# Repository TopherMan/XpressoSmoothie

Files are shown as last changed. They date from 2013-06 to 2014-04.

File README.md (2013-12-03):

Overview
========
This is a plan to make a RepRap electronics solution capable of running the Smoothie firmware. The board will be built around the LPCXpresso 1769, with a more modular design in the spirit of RAMPS. More information about the RepRap project can be found at http://reprap.org, and more information about Smoothie can be found at http://smoothieware.org.

Features
========
* 120 MHz ARM Cortex-M3 processor, chosen to run the highly efficent and modular Smoothie firmware (https://github.com/arthurwolf/Smoothie).
* Can be powered by 12V or 24V.
* 5 Axes, using Pololu A4988-style stepper drivers.
* 4 Power output MOSFETs, two with automotive blade-style fuses for bed and heater over-current protection.
* 6 endstops and 3 thermistors.
* Integrated microSD reader.
* Pins broken out for SPI, I2C, GPIO, and on-board Ethernet chip for future expansion.
* Due to the modular nature of Smoothie, the board should also work with mills, laser cutters, and any future modules.

Current Status
==============
Revision 0 boards had issues due to pins being assigned to ports hard-coded to other purposes in Smoothie. Revision 1 had issues due to pin assignment changes in the Smoothie firmware. Revision 2 is close to complete, with pinout verification needed.

Opto Endstops
=============
Noobman is finalizing designs for a small seperate opto board.

Bill of Materials -- NOTE: may need to be updated
=================
Two bill of material files are included. BOM.ods lists the individual components and their corresponding Digikey part numbers. BOM_Digikey.xls is formatted for uploading directly to Digikey. There are three columns available, one for the complete range of parts, one for everything except opto circuitry (though the difference is only 6 resistors), and one without opto circuitry or headers, so you can use big cheap strips of breakaway headers.

To Use
======
Assembly instructions will be made with the alpha board.
Flashing the bootloader and getting Smoothie on the LPCXpresso can be found at http://smoothieware.org/smoothie-on-a-breadboard.

More Information
================
Wiki page at http://reprap.org/wiki/Xpresso_Smoothie.

Authors
=======
TopherMan (Chris George) -- Initial design idea and basic layout, as well as testing and assembly.
Noobman -- Significant input on design, and completed nearly all routing.
Bobc -- kicad libraries are borrowed from his repo here: https://github.com/bobc/bobc_hardware Additionally, blade fuse usage based on his design for RAMPS_FD

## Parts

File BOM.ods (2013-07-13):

Reference | Value | Footprint | Digikey | Alternate Piece
C1 | 100u | c_elec_6.3x7.7 | PCE4238CT-ND
C2 | 100u | c_elec_6.3x7.7 | PCE4238CT-ND
C3 | 100u | c_elec_6.3x7.7 | PCE4238CT-ND
C4 | 100u | c_elec_6.3x7.7 | PCE4238CT-ND
C5 | 1u/50v | SM1206 | 1276-1068-1-ND
C6 | 1u/50v | SM1206 | 1276-1068-1-ND
C7 | 1u/50v | SM1206 | 1276-1068-1-ND
C8 | 1u/50v | SM1206 | 1276-1068-1-ND
C9 | 10u | c_elec_4x5.3 | PCE3878CT-ND
C10 | 10u | c_elec_4x5.3 | PCE3878CT-ND
C11 | 10u | c_elec_4x5.3 | PCE3878CT-ND
C12 | 100u | c_elec_6.3x7.7 | PCE4238CT-ND
C13 | 100u | c_elec_6.3x7.7 | PCE4238CT-ND
C14 | 100u | c_elec_6.3x7.7 | PCE4238CT-ND
C15 | 220n | SM0805 | 1276-2948-1-ND
C16 | 220n | SM0805 | 1276-2948-1-ND
C17 | 220n | SM0805 | 1276-2948-1-ND
C18 | 220n | SM0805 | 1276-2948-1-ND
C19 | 220n | SM0805 | 1276-2948-1-ND
C20 | 220n | SM0805 | 1276-2948-1-ND
C21 | 220n | SM0805 | 1276-2948-1-ND
C22 | 1u/50v | SM1206 | 1276-1068-1-ND
C23 | 1u/50v | SM1206 | 1276-1068-1-ND
C24 | 1u/50v | SM1206 | 1276-1068-1-ND
D1 | 1N4007 | DO-41 | 641-1312-1-ND
D2 | 1N4007 | DO-41 | 641-1312-1-ND
D3 | POWER_1 | LED_0805 | 475-1415-1-ND
D4 | POWER_2 | LED_0805 | 475-1415-1-ND
D5 | POWER_3 | LED_0805 | 475-1415-1-ND
D6 | POWER_4 | LED_0805 | 475-1415-1-ND
D7 | 1N4007 | DO-41 | 641-1312-1-ND
D8 | 1N4007 | DO-41 | 641-1312-1-ND
D10 | V_IN | LED_0805 | 475-1410-1-ND
D11 | V_GATES | LED_0805 | 475-1410-1-ND
D12 | 3V3 | LED_0805 | 475-1410-1-ND
F1 | FUSE | MF-R1100 | RGEF1100-ND
F2 | FUSE | MF-R500 | MF-R500-ND
J1 | HEADER_4 | PIN_ARRAY_4x1 | 3M9449-ND
J2 | HEADER_4 | PIN_ARRAY_4x1 | 3M9449-ND
J3 | HEADER_3 | PIN_ARRAY_3x1 | 3M9448-ND
J4 | HEADER_3X2 | PIN_ARRAY_3x2 | 3M9459-ND
J5 | HEADER_3X2 | PIN_ARRAY_3x2 | 3M9459-ND
J6 | LPCXPRESSO | 2X PIN_ARRAY 27X1 | SAM1213-27-ND
 |  |  | SAM1213-27-ND
J7 | HEADER_4 | PIN_ARRAY_4x1 | 3M9449-ND
J8 | HEADER_4 | PIN_ARRAY_4x1 | 3M9449-ND
J9 | HEADER_3X2 | PIN_ARRAY_3x2 | 3M9459-ND
J10 | HEADER_3X2 | PIN_ARRAY_3x2 | 3M9459-ND
J11 | Pwr_in | Power Block | WM7855-ND | WM7847-ND
J12 | HEADER_4 | PIN_ARRAY_4x1 | 3M9449-ND
J13 | HEADER_4X2 | pin_array_4x2 | 3M9458-ND
J14 | HEADER_3X2 | PIN_ARRAY_3x2 | 3M9459-ND
J15 | HEADER_4 | PIN_ARRAY_4x1 | 3M9449-ND
J16 | HEADER_4 | PIN_ARRAY_4x1 | 3M9449-ND
J17 | HEADER_4 | PIN_ARRAY_4x1 | 3M9449-ND
J18 | HEADER_4 | PIN_ARRAY_4x1 | 3M9449-ND
J19 | HEADER_2 | LARGE_2x1 | WM7853-ND
J20 | HEADER_2 | LARGE_2x1 | WM7853-ND
J21 | HEADER_2 | LARGE_2x1 | WM7853-ND
J22 | HEADER_2 | LARGE_2x1 | WM7853-ND
J23 | HEADER_4 | PIN_ARRAY_4x1 | 3M9449-ND
J24 | HEADER_4 | PIN_ARRAY_4x1 | 3M9449-ND
J25 | HEADER_4 | PIN_ARRAY_4x1 | 3M9449-ND
J26 | USB | USB_MICRO | 609-4048-1-ND
J27 | HEADER_4 | PIN_ARRAY_4x1 | 3M9449-ND
J28 | CONN_MICROSD | MICROSD | H11610CT-ND
 | HEADER_4 | PIN_ARRAY_4x1 | 3M9449-ND
J172 | HEADER_2 | PIN_ARRAY_2x1 | 3M9447-ND
J232 | HEADER_2 | PIN_ARRAY_2x1 | 3M9447-ND
J252 | HEADER_2 | PIN_ARRAY_2x1 | 3M9447-ND
JP1 | HEADER_2 | PIN_ARRAY_2x1 | 3M9447-ND
JP2 | HEADER_2 | PIN_ARRAY_2x1 | 3M9447-ND
JP3 | HEADER_2 | PIN_ARRAY_2x1 | 3M9447-ND
JP4 | HEADER_2 | PIN_ARRAY_2x1 | 3M9447-ND
 | HEADER_2 | PIN_ARRAY_2x1 | 3M9447-ND
 | HEADER_2 | PIN_ARRAY_2x1 | 3M9447-ND
 | HEADER_2 | PIN_ARRAY_2x1 | 3M9447-ND
 | HEADER_2 | PIN_ARRAY_2x1 | 3M9447-ND
JP5 | HEADER_2 | PIN_ARRAY_2x1 | 3M9447-ND
Q1 | IRLB 8743 | TO-220 | IRLB8743PBF-ND
Q2 | IRLB 8743 | TO-220 | IRLB8743PBF-ND
Q3 | IRLB 8743 | TO-220 | IRLB8743PBF-ND
Q4 | IRLB 8743 | TO-220 | IRLB8743PBF-ND
R1 | 4k7 | SM0805 | RHM4.70KAECT-ND
R2 | 4k7 | SM0805 | RHM4.70KAECT-ND
R3 | 1k | SM0805 | RHM1.0KKCT-ND
R4 | 1k | SM0805 | RHM1.0KKCT-ND
R5 | 4k7 | SM0805 | RHM4.70KAECT-ND
R6 | 4k7 | SM0805 | RHM4.70KAECT-ND
R7 | 100r | SM0805 | RHM100KCT-ND
R8 | 1k | SM0805 | RHM1.0KKCT-ND
R9 | 1k | SM0805 | RHM1.0KKCT-ND
R10 | 4k7 | SM0805 | RHM4.70KAECT-ND
R11 | 4k7 | SM0805 | RHM4.70KAECT-ND
R12 | 4k7 | SM0805 | RHM4.70KAECT-ND
R13 | 4k7 | SM0805 | RHM4.70KAECT-ND
R14 | 1k | SM0805 | RHM1.0KKCT-ND
R15 | 100r | SM0805 | RHM100KCT-ND
R16 | 100r | SM0805 | RHM100KCT-ND
R18 | 1k8 | SM0805 | RHM1.8KKCT-ND
R19 | 1k8 | SM0805 | RHM1.8KKCT-ND
R21 | 1k8 | SM0805 | RHM1.8KKCT-ND
R23 | 1k8 | SM0805 | RHM1.8KKCT-ND
R24 | 100r | SM0805 | RHM100KCT-ND
R25 | 100r | SM0805 | RHM100KCT-ND
R28 | 1k8 | SM0805 | RHM1.8KKCT-ND
R29 | 680r | SM0805 | RHM680KCT-ND
R30 | 100r | SM0805 | RHM100KCT-ND
RL_diode1 | 100r | SM0805 | RHM100KCT-ND | Values may change based on opto used
RL_diode2 | 100r | SM0805 | RHM100KCT-ND | Values may change based on opto used
RL_diode3 | 100r | SM0805 | RHM100KCT-ND | Values may change based on opto used
Rp_rcv1 | 1k5 | SM0805 | RHM1.5KKCT-ND | Values may change based on opto used
Rp_rcv2 | 1k5 | SM0805 | RHM1.5KKCT-ND | Values may change based on opto used
Rp_rcv3 | 1k5 | SM0805 | RHM1.5KKCT-ND | Values may change based on opto used
SW1 | SW_PUSH | SW_PUSH_SMALL | 450-1642-ND
SW2 | SW_PUSH | SW_PUSH_SMALL | 450-1642-ND
 | SW_PUSH | SW_PUSH_SMALL | 450-1650-ND
Th0 | CONN_2 | PIN_ARRAY_2x1 | 3M9447-ND
Th1 | CONN_2 | PIN_ARRAY_2x1 | 3M9447-ND
Th2 | CONN_2 | PIN_ARRAY_2x1 | 3M9447-ND
U1 | POLOLU_A4988 | 2X PIN_ARRAY 8X1 | S7006-ND
 |  |  | S7006-ND
U2 | POLOLU_A4988 | 2X PIN_ARRAY 8X1 | S7006-ND
 |  |  | S7006-ND
U3 | POLOLU_A4988 | 2X PIN_ARRAY 8X1 | S7006-ND
 |  |  | S7006-ND
U4 | POLOLU_A4988 | 2X PIN_ARRAY 8X1 | S7006-ND
 |  |  | S7006-ND
U5 | POLOLU_A4988 | 2X PIN_ARRAY 8X1 | S7006-ND
 |  |  | S7006-ND
U7 | LM7809CT | TO-220 | LM7809CT-ND
U8 | TC4422A | SO8N | TC4422AVOA-ND
U9 | TC4422A | SO8N | TC4422AVOA-ND
U10 | TC4422A | SO8N | TC4422AVOA-ND
U11 | TC4422A | SO8N | TC4422AVOA-ND
U12 | LM1117-3.3 | SOT223 | LM1117IMPX-3.3/NOPBCT-ND
 | Jumpers | 2 pos | A26228-ND | You'll need 19 for full microstepping on all 5 axes and all mcu jumpers set for LPCXpresso and 20 for mbed

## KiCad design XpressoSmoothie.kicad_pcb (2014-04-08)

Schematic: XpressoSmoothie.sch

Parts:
C1, C2, C3, C4, C12, C13, C14: 100u
C5, C7, C23, C24: 1u/50v
C6, C8: 1u/50v; SM1206
C9, C10, C11: 10u
C15, C16, C17, C18, C19, C20, C21: 220n
C22: 1u; SM1206
D1, D2, D7, D8: 1N4007
D3: POWER_1
D4: POWER_2
D5: POWER_3
D6: POWER_4
D9: LED4
D11: V_GATES
D12: 3V3
D13: LED2
D14: LED3
D15: LED1
F1, F2: FUSE
Hole1, Hole2, Hole3, Hole4: CONN_1
J1, J2, J7, J8, J12, J15, J27, J29, J30: HEADER_4
J3, J16, J17, J18, J23, J24, J25: HEADER_3
J4, J5, J9, J10, J14: HEADER_3X2
J6: LPCXPRESSO_1769_HEADER
J11: Pwr_in
J13: HEADER_6
J19, J20, J21, J22: HEADER_2
J26: USB
J28: MICROSD-MOLEX
M1: LOGO_OSHW; OSHW_logo_large
M2: LOGO_OSHW; OSHW_logo_10
Q1, Q2, Q3, Q4: IRLB 8743
R1, R2, R5, R6, R10, R11, R12, R13: 4k7
R3, R4, R8, R9, R14: 1k
R7, R15, R16, R17, R20, R22, R24, R25, R26, R30: 100
R18, R19, R21, R23: 1k8
R27, R28, R31, R32: 10k
R29: 680
SW1, SW2, SW3: SW_PUSH
Th0, Th1, Th2: CONN_2
U1, U2, U3, U4, U5: POLOLU_A4988
U7: LM7809CT; TO-220
U8, U9, U10, U11: TC4422A
U12: LM1117-3.3; TO-220

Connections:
*32_RD-: J6.32, J27.4
*33_RD+: J6.33, J27.3
*34_TD-: J6.34, J27.2
*35_TD+: J6.35, J27.1
*Bootloader: J6.51, SW3.1
*CS: J6.8, J28.2
*CS0: J6.14, J30.4
*LED1: J6.101, R20.2
*LED2: J6.102, R26.2
*LED3: J6.103, R17.2
*LED4: J6.104, R22.2
*MISO: J6.6, J28.7
*MISO0: J6.12, J30.2
*MOSI: J6.5, J28.3
*MOSI0: J6.11, J30.1
*PLAY/PAUSE: J6.53, SW2.1
*PLAY_LED: J6.115
*RESET: J6.4, SW1.1
*RX: J6.21, J29.4
*SCK: J6.7, J28.5
*SCK0: J6.13, J30.3
*SCL0: J6.26, J15.4
*SDA0: J6.25, J15.3
*THERM0: C11.1, J6.15, R12.1, Th0.1
*THERM1: C10.1, J6.16, R11.1, Th1.1
*THERM2: C9.1, J6.17, R10.1, Th2.1
*TX: J6.22, J29.3
*USB-D+: J6.37, J26.3 (D+)
*USB-D-: J6.36, J26.2 (D-)
*USB_SOFT_CONNECT: J6.119
+3.3VP: C14.1, C16.1, C22.1, J6.28, J15.1, J16.1, J17.1, J18.1, J23.1, J24.1, J25.1, J28.4, J29.2, R3.2, R4.2, R7.1, R8.2, R9.2, R10.2, R11.2, R12.2, R14.2, R15.1, R16.1, R24.1, R25.1, R30.2, U12.2 (OUT)
+5V: J3.3, J13.1, J26.1 (Vbus)
/THERM3: J6.18
A-DIR: J6.38, U5.16 (DIR)
A-EN: J6.39, R13.2, U5.9 (EN)
A-STEP: J6.42, U5.15 (STEP)
B-DIR: J6.117, U1.16 (DIR)
B-EN: J6.116, R1.2, U1.9 (EN)
B-STEP: J6.50, U1.15 (STEP)
BUZZ: J6.20, J13.5
CLICK: J6.19, J13.3
ENC_A: J6.105, J13.6
ENC_B: J6.106, J13.4
GND: C1.2, C2.2, C3.2, C4.2, C8.2, C9.2, C10.2, C11.2, C12.2, C13.2, C14.2, C15.2, C16.2, C17.2, C18.2, C19.2, C20.2, C21.2, C22.2, D9.2 (K), D12.2 (K), D13.2 (K), D14.2 (K), D15.2 (K), J6.1, J6.54, J11.3, J15.2, J16.2, J17.2, J18.2, J23.2, J24.2, J25.2, J26.4 (GND), J26.5 (Shield_1), J26.6 (Shield_2), J28.6, J28.GND, J28.POL, J29.1, R27.1, R28.1, R31.1, R32.1, SW1.2, SW2.2, SW3.2, Th0.2 (PM), Th1.2 (PM), Th2.2 (PM), U1.1 (GND), U1.7 (GND), U2.1 (GND), U2.7 (GND), U3.1 (GND), U3.7 (GND), U4.1 (GND), U4.7 (GND), U5.1 (GND), U5.7 (GND), U7.2 (GND), U12.1 (ADJ)
GNDPWR: C5.2, C6.2, C7.2, C23.2, C24.2, J11.2, Q1.S, Q2.S, Q3.S, Q4.S, R29.1, U8.4 (GND), U8.5 (GND), U9.4 (GND), U9.5 (GND), U10.4 (GND), U10.5 (GND), U11.4 (GND), U11.5 (GND)
unnamed: J10.5, U4.12 (MS3)
unnamed: J10.1, U4.10 (MS1)
unnamed: J8.4, U4.6 (2B)
unnamed: J8.1, U4.3 (IB)
unnamed: J8.2, U4.4 (1A)
unnamed: J8.3, U4.5 (2A)
unnamed: J10.3, U4.11 (MS2)
unnamed: J14.2, J14.4, J14.6, R13.1, R14.1, U5.13 (RST), U5.14 (SLP)
unnamed: J10.2, J10.4, J10.6, R6.1, R9.1, U4.13 (RST), U4.14 (SLP)
unnamed: J14.5, U5.12 (MS3)
unnamed: J14.1, U5.10 (MS1)
unnamed: J12.4, U5.6 (2B)
unnamed: J12.1, U5.3 (IB)
unnamed: J12.2, U5.4 (1A)
unnamed: J12.3, U5.5 (2A)
unnamed: J14.3, U5.11 (MS2)
unnamed: D2.1 (A), D4.2 (K), J20.1, Q2.D
unnamed: Q2.G, U9.6 (OUT), U9.7 (OUT)
unnamed: D4.1 (A), R21.2
unnamed: J5.2, J5.4, J5.6, R2.1, R4.1, U2.13 (RST), U2.14 (SLP)
unnamed: D1.1 (A), D3.2 (K), J19.1, Q1.D
unnamed: Q1.G, U8.6 (OUT), U8.7 (OUT)
unnamed: D3.1 (A), R19.2
unnamed: J9.5, U3.12 (MS3)
unnamed: J9.1, U3.10 (MS1)
unnamed: J7.4, U3.6 (2B)
unnamed: J7.1, U3.3 (IB)
unnamed: J7.2, U3.4 (1A)
unnamed: J7.3, U3.5 (2A)
unnamed: J9.3, U3.11 (MS2)
unnamed: J9.2, J9.4, J9.6, R5.1, R8.1, U3.13 (RST), U3.14 (SLP)
unnamed: J5.5, U2.12 (MS3)
unnamed: J5.1, U2.10 (MS1)
unnamed: J2.4, U2.6 (2B)
unnamed: J2.1, U2.3 (IB)
unnamed: J2.2, U2.4 (1A)
unnamed: J2.3, U2.5 (2A)
unnamed: J5.3, U2.11 (MS2)
unnamed: D9.1 (A), R22.1
unnamed: D14.1 (A), R17.1
unnamed: D13.1 (A), R26.1
unnamed: D15.1 (A), R20.1
unnamed: J3.2, U12.3 (IN)
unnamed: F1.2, J19.2
unnamed: F2.2, J20.2
unnamed: D11.2 (K), R29.2
unnamed: D6.2 (K), D7.1 (A), J22.1, Q4.D
unnamed: Q4.G, U10.6 (OUT), U10.7 (OUT)
unnamed: D6.1 (A), R18.2
unnamed: D5.2 (K), D8.1 (A), J21.1, Q3.D
unnamed: Q3.G, U11.6 (OUT), U11.7 (OUT)
unnamed: D5.1 (A), R23.2
unnamed: D12.1 (A), R30.1
unnamed: J4.5, U1.12 (MS3)
unnamed: J4.1, U1.10 (MS1)
unnamed: J1.4, U1.6 (2B)
unnamed: J1.1, U1.3 (IB)
unnamed: J1.2, U1.4 (1A)
unnamed: J1.3, U1.5 (2A)
unnamed: J4.3, U1.11 (MS2)
unnamed: J4.2, J4.4, J4.6, R1.1, R3.1, U1.13 (RST), U1.14 (SLP)
unnamed: R15.2, U2.2 (VDD)
unnamed: R16.2, U3.2 (VDD)
unnamed: R24.2, U4.2 (VDD)
unnamed: R25.2, U5.2 (VDD)
unnamed: R7.2, U1.2 (VDD)
PANEL_KILL: J6.52, J13.2
POWER1: J6.49, R27.2, U8.2 (IN)
POWER2: J6.48, R28.2, U9.2 (IN)
POWER3: J6.47, R31.2, U11.2 (IN)
POWER4: J6.113, R32.2, U10.2 (IN)
PS-ON: J6.46
SD_card_detect: J28.DET
Vgates: C5.1, C7.1, C13.1, C15.1, C23.1, C24.1, D11.1 (A), J3.1, U7.3 (OUT), U8.1 (VDD), U8.8 (VDD), U9.1 (VDD), U9.8 (VDD), U10.1 (VDD), U10.8 (VDD), U11.1 (VDD), U11.8 (VDD)
Vin_Hi_curr: C6.1, D1.2 (K), D2.2 (K), D7.2 (K), D8.2 (K), F1.1, F2.1, J11.1, J21.2, J22.2, R18.1, R19.1, R21.1, R23.1
Vin_rmot: C1.1, C2.1, C3.1, C4.1, C8.1, C12.1, C17.1, C18.1, C19.1, C20.1, C21.1, J11.4, U1.8 (VMOT), U2.8 (VMOT), U3.8 (VMOT), U4.8 (VMOT), U5.8 (VMOT), U7.1 (IN)
X-DIR: J6.118, U2.16 (DIR)
X-EN: J6.27, R2.2, U2.9 (EN)
X-STEP: J6.45, U2.15 (STEP)
XMAX: J6.108, J24.3
XMIN: J6.107, J17.3
Y-DIR: J6.23, U3.16 (DIR)
Y-EN: J6.24, R5.2, U3.9 (EN)
Y-STEP: J6.44, U3.15 (STEP)
YMAX: J6.114, J25.3
YMIN: J6.109, J18.3
Z-DIR: J6.40, U4.16 (DIR)
Z-EN: J6.41, R6.2, U4.9 (EN)
Z-STEP: J6.43, U4.15 (STEP)
ZMAX: J6.110, J23.3
ZMIN: J6.111, J16.3

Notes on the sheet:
POWER
MOSFETS
Output connectors are V+ and GND. Q1 is bed mosfet to keep high current trace short. Solder a thick copper wire from input to Q1 and back.
Enstops and Thermistors
STEPPER DRIVERS
SD card
I2C
Expansion
USB
Miscellaneous
Pololu drivers or compatible footprint: http://www.pololu.com/catalog/category/120
MOS drivers TC4452 (SOIC-8-Narrow) or TC4422A (SOIC-8-WIDE), check and adjust pcb footprint if needed.
Components: all smd ceramic caps dielectric X5R or X7R or better, leds: 20mA. Mosfet output connectors are V+ and GND. Q1 is bed mosfet to keep high current trace short. Solder a thick copper wire from input to Q1 and back (both on V+ and gnd) to help with the high current. For DIY purposes increas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
LPCXpresso 1769
Power in: 12V to 28V The two input connector voltages must come from same psu (same gnd), though may have different values.
Vin_Hi_curr does not have led indicator
Regulators have different pin numbering If Vin_r is 12V then Vgates are 12V-2Vdroput= 10V
Ethernet
Serial
*NOTE: Labels starting with * are hard-coded to a specific use and cannot be reassigned.
NOTE: Pins 9 and 10 are hard-coded in Smoothie for I2C communication with current-sense chips.
SPI
PANEL
LED1 init done, LED2 main loop LED3 idle loop, LED4 SD okay

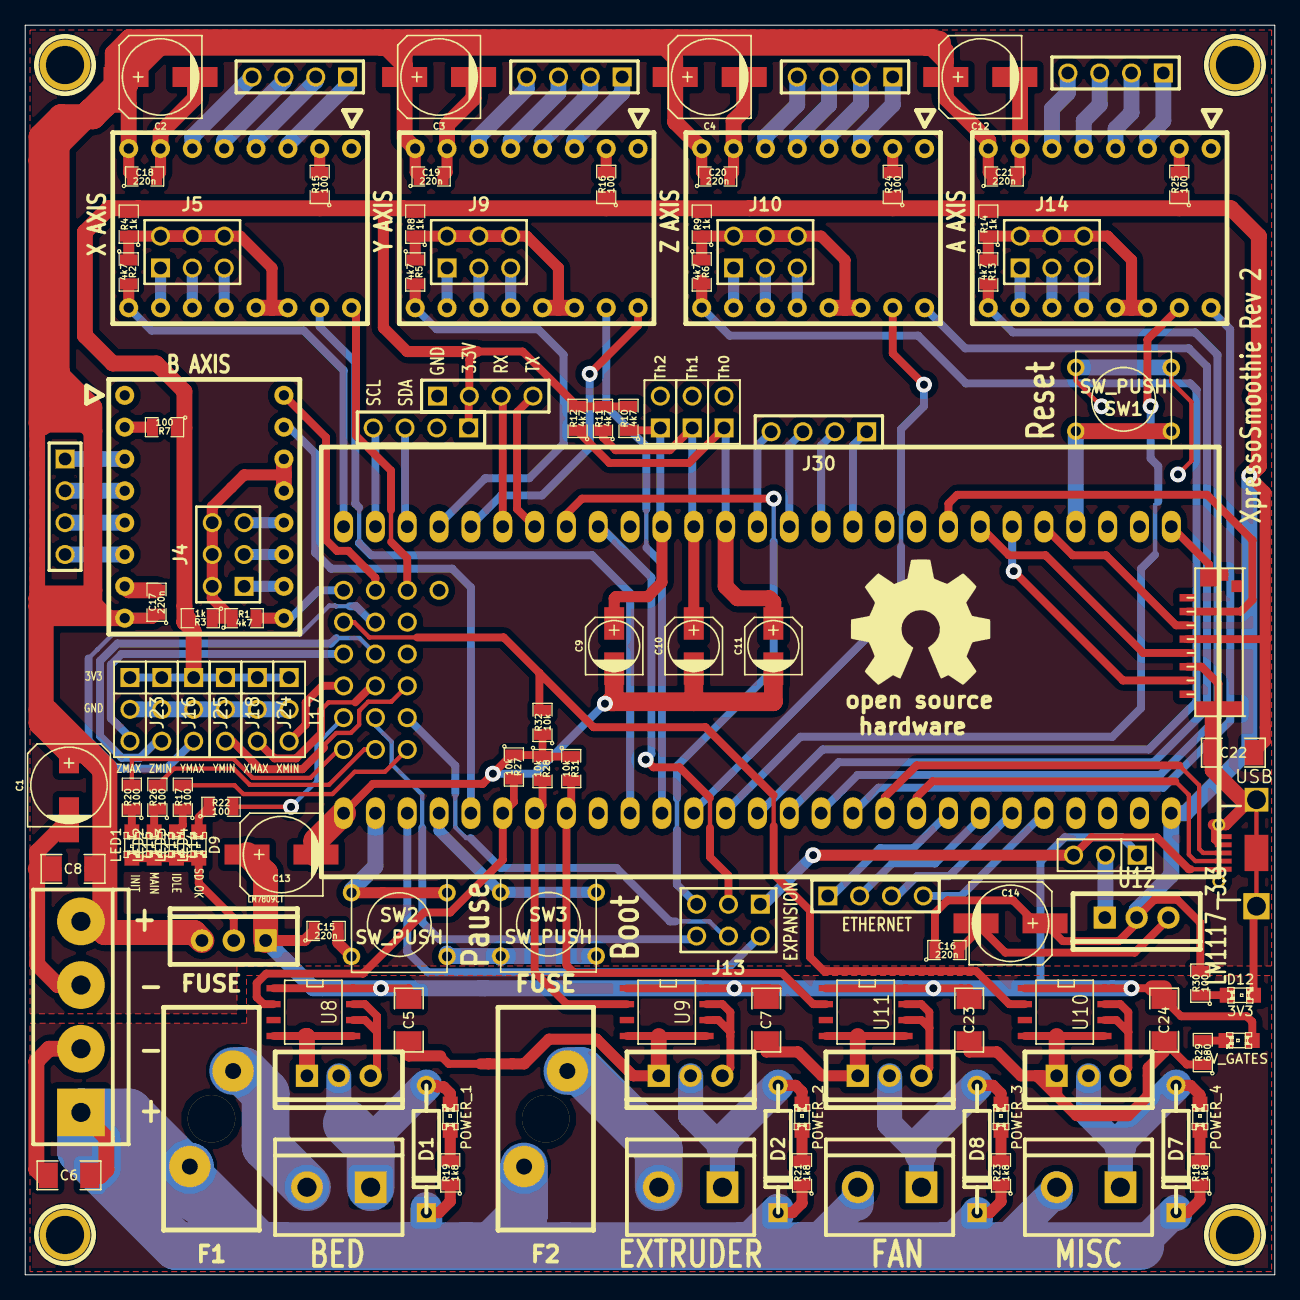
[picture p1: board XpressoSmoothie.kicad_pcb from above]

Board: 2 copper layers, 99.7 x 99.7 mm, 129 parts (1 on the bottom side), 131 nets.

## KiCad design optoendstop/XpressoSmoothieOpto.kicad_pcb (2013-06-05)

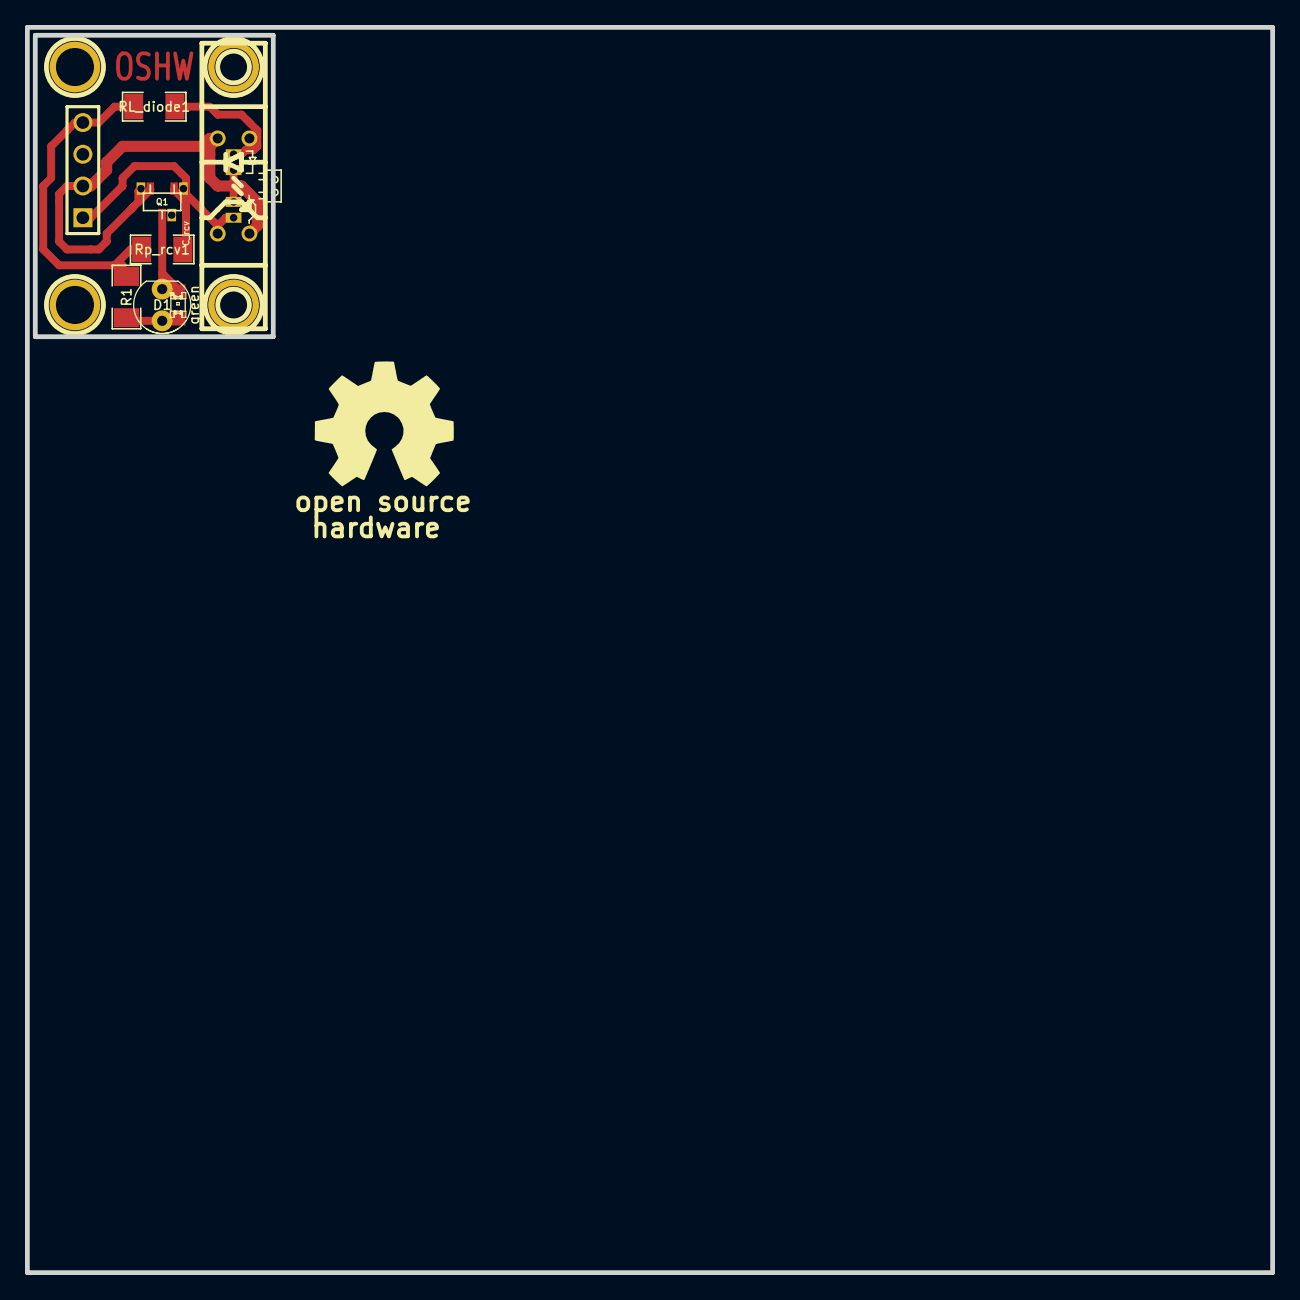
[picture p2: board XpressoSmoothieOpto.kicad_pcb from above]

Board: 2 copper layers, 99.7 x 99.7 mm, 13 parts (0 on the bottom side), 6 nets.

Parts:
D1: green; LED-0805-3MM
Hole1, Hole2, Hole3, Hole4: CONN_1; 1pin
IC1: TCST1103; TCST1103-2103
IC11: TCST1103; TCRT1000
J1: HEADER_4; PIN_ARRAY_4x1
M2: LOGO_OSHW; OSHW_logo_2
Q1: BS108D; sot23-to92
R1: 150; SM1206
RL_diode1: 68; SM1206
Rp_rcv1: 1k5; SM1206

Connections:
3.3V: J1.4, R1.2, RL_diode1.2, Rp_rcv1.1
GND: IC1.E/D, IC1.K/E, IC11.E/D, IC11.K/E, J1.2, Q1.S
unnamed: D1.1, R1.1
unnamed: D1.2, Q1.D
unnamed: IC1.A/+, IC11.A/+, RL_diode1.1
Signal1: IC1.C/+, IC11.C/+, J1.1, Q1.G, Rp_rcv1.2

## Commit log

2013-05-12 Initial commit. Schematic only missing mosfets.
    [XpressoSmoothie.sch]
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2013-05-13 Switch around pins and add pins for UART. Finish most of netlist.
    [XpressoSmoothie.brd, XpressoSmoothie.sch]
2013-05-13 Minor tag issues.
    [XpressoSmoothie.sch]
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2013-05-14 Add screw terminal .mod file, plus tons of fixes/layout changes.
    [XpressoSmoothie.brd, XpressoSmoothie.sch]
2013-05-14 Working on layout. Needed to move from 5cmx10cm to 10cmx10cm.
    [XpressoSmoothie.brd]
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2013-05-14 Switch out header for proper SD card connector.
    [XpressoSmoothie.brd, XpressoSmoothie.sch]
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2013-05-15 Bunch of tracks made. A few minor label issues fixed.
    [XpressoSmoothie.brd, XpressoSmoothie.sch]
2013-05-15 Finished most of the tracks. Need to add some stuff.
    [XpressoSmoothie.brd]
2013-05-15 Add LM1117 and jumper to power from 12V or from USB.
    [XpressoSmoothie.sch]
2013-05-15 Fixed stupid labelling error.
    [XpressoSmoothie.brd, XpressoSmoothie.sch]
2013-05-15 Finished layout attempt 1. Will probably add I2C header in a bit.
    [XpressoSmoothie.brd]
2013-05-15 D'oh, made everything fit within 10cmx10cm envelope. Added some labels.
    [XpressoSmoothie.brd]
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2013-05-16 Fixed FETs so that they're non-inverting.
    [XpressoSmoothie.sch]
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2013-05-16 Fixed up netlist and footprints, being layout attempt 2.
    [XpressoSmoothie.dsn, XpressoSmoothie.sch]
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2013-05-18 Trying with the LPCXpresso turned the other way. Maybe this will work a bit smoother.
    [XpressoSmoothie.brd, XpressoSmoothie.sch]
2013-05-18 Fixed the pinout to something that makes sense for the new orientation. Also, going to bed.
    [XpressoSmoothie.brd, XpressoSmoothie.sch]
2013-05-18 preliminary schematic structure, annotation changes
    organizing, few additions and deletions, annotation changed
    added notes of few things to be sorted later
    [XpressoSmoothie.sch]
2013-05-18 Change around voltage select for powering the board. Fixes #2.
    [XpressoSmoothie.sch]
2013-05-18 Updated footprints, netlist, and got board ready for placing parts. I think I need to update the SD card reader footprint; it's missing pad 10 and is based on 3M's design which isn't manufactured any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
    [XpressoSmoothie.brd, XpressoSmoothie.sch]
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2013-05-19 brd file kicad_pcb, layout attempt
    changed pcb file from brd to *.kicad_pcb extension, few schematic
    changes and attempted a layout
    [XpressoSmoothie.kicad_pcb, XpressoSmoothie.sch]
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2013-05-19 stiching up routes for module
    routes that need to be checked from blocks to module
    [XpressoSmoothie.kicad_pcb, XpressoSmoothie.sch]
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2013-05-19 step line moved from pin24 (p0.22)
    and changed pin24 (p0.22) to enable xy
    [XpressoSmoothie.kicad_pcb, XpressoSmoothie.sch]
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2013-05-20 Missed a connection on Q1, and moved C8 so it doesn't overlab C1.
    [XpressoSmoothie.kicad_pcb]
2013-05-20 Changed the order of the steppers so that B is off on its own instead of X.
    [XpressoSmoothie.kicad_pcb, XpressoSmoothie.sch]
2013-05-20 Missed a connection.
    [XpressoSmoothie.kicad_pcb]
2013-05-21 pin allocation, drivers again
    needed pin changes to x and y can have same enable while being in same
    line for wiring, driver changed, polished schematic, board still needs
    small tweaks
    [XpressoSmoothie.kicad_pcb, XpressoSmoothie.sch]
2013-05-21 footprint text correction
    [XpressoSmoothie.kicad_pcb, XpressoSmoothie.sch]
2013-05-21 spaced the 4 pololu on top
    spaced the 4 pololu on top
    [XpressoSmoothie.kicad_pcb, XpressoSmoothie.sch]
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2013-05-21 Added Open Source Hardware logos on front and back, and added board name and rev number to front.
    [XpressoSmoothie.kicad_pcb]
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2013-05-21 Labels and values cleaned. All the important stuff is clearly labeled, and all small labels and values are visible and non-overlapping.
    [XpressoSmoothie.kicad_pcb]
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2013-05-23 Fixed the logos so that they were added the proper way, with a placeholder in the schematic. Fixes #6.
    [XpressoSmoothie.kicad_pcb, XpressoSmoothie.sch]
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2013-05-24 Hid more labels, added some in so that everything is clearly marked and there are no overlaps.
    [XpressoSmoothie.kicad_pcb, XpressoSmoothie.sch]
2013-05-24 Adjusted clearance for pads/vias/tracks to 0.2 mm. Still within allowed tolerances for Seeedstudio (and probably other fab houses), but stops the DRC from complaining.
    [XpressoSmoothie.kicad_pcb]
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2013-05-28 Got Digikey numbers for everything except resistors. Need to verify values first.
    [XpressoSmoothie.ods]
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2013-05-28 Adjusted BOM and added .xls file formatted to upload straight to Digikey.
    [XpressoSmoothie.ods, XpressoSmoothie.xls]
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2013-05-29 Fixed resistor values.
    [XpressoSmoothie.kicad_pcb, XpressoSmoothie.sch]
2013-05-29 Fixed Molex MicroSD holder. Closes #8.
    [XpressoSmoothie.kicad_pcb]
2013-05-29 shifted uSD
    shifted uSD holder more to the edge, changed resistor values (yet again)
    [XpressoSmoothie.kicad_pcb, XpressoSmoothie.sch]
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2013-05-29 Fixed a few minor errors in BOM, updated BOM_Digikey with proper numbers, as well as descriptions. Closes #10.
    [BOM.ods, BOM_Digikey.xls]
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2013-05-30 mos4 pwm fix
    mos 4 pwm
    [XpressoSmoothie.kicad_pcb, XpressoSmoothie.sch]
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2013-05-31 Oh, duh. Since the VIN pin isn't connected to anything on the Xpresso, it doesn't need a jumper. I can just put 5V on that pin for the mbed and that Xpresso won't be hurt.
    [XpressoSmoothie.sch]
2013-05-31 Fixed the 5V trace on the board.
    [XpressoSmoothie.kicad_pcb]
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2013-06-01 Fixed up jumpers. Removed an extra, removed sd_detect so that x and y enable are seperate, and added one so they are joined together. Closes #14.
    [XpressoSmoothie.kicad_pcb, XpressoSmoothie.sch]
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2013-06-02 Reset to using SD detect.
    [XpressoSmoothie.kicad_pcb, XpressoSmoothie.sch]
2013-06-02 Reverted back to using SD detect. Added jumper to connect/disconnect 5V line to USB Vbus. I think this finally means we're compatible with the mbed, so closing #11 again.
    [XpressoSmoothie.kicad_pcb, XpressoSmoothie.sch]
2013-06-02 Fixed up fuses (which were hanging slightly over the edge) and thinned edge graphics for clarity.
    [XpressoSmoothie.kicad_pcb]
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2013-06-02 Moved USB so that PCB edge line lines up with the edge of the PCB. Also removed silkscreen lines that hung over the edge. Closes #15.
    [XpressoSmoothie.kicad_pcb]
2013-06-02 Moved some traces and text so that there is a minimum of 10 mil clearnace between any traces or pads and the pcb edge. Closes #16.
    [XpressoSmoothie.kicad_pcb]
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2013-06-02 D'oh, cut the 3.3v line to card reader. Fixed.
    [XpressoSmoothie.kicad_pcb]
2013-06-02 Switched around endstop names so they're in order going top to bottom.
    [XpressoSmoothie.kicad_pcb, XpressoSmoothie.sch]
2013-06-02 First set of gerbers created. Barring major catastrophe, they will be sent off tomorrow for fabrication.
    [XpressoSmoothie.kicad_pcb]
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2013-06-03 Updated BOM to reflect all recent changes. Now up-to-date with the board.
    [BOM.ods]
2013-06-03 Updated BOM_Digikey, and added no opto and no header options for ease of use.
    [BOM_Digikey.xls]
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2013-06-04 oe_clearance
    optoendstops clearance check
    [XpressoSmoothieOpto.kicad_pcb]
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2013-06-20 Switch micro USB Digikey part number in BOM. Original one was upside-down from what we needed. Closes #22.
    [BOM.ods, BOM_Digikey.xls]
2013-06-20 Change 11A fuse footprint to MF-R500 (5A footprint) since that's what fits. Closes #21
    [XpressoSmoothie.kicad_pcb]
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2013-07-09 All jumpers added to schematic, so it should all be set for mbed and for LPCXpresso. Time to start routing.
    [XpressoSmoothie.sch]
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2013-07-10 Added notes on silkscreen for jumpers. After one or two additional checks, I'll officially call it revision 1.
    [XpressoSmoothie.kicad_pcb]
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2013-07-13 Updated schematic so that pins hard-coded to a specific purpose have a label beginning with * as recommended in #20.
    [XpressoSmoothie.kicad_pcb, XpressoSmoothie.sch]
2013-07-13 Realized it makes more sense to tie XYZ enables together for mbed instead of XYA. An mbed user would be able to do filament changes by jogging the head to a new position, disabling A, changing filame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
    [XpressoSmoothie.kicad_pcb, XpressoSmoothie.sch]
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2013-12-02 Replace polyfuses with auto blade fuses, imitating RAMPS-FD
    [XpressoSmoothie.kicad_pcb]
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2013-12-03 Bunch of routing. A few pin reassignments, make sure to adjust example config file.
    [XpressoSmoothie.kicad_pcb, XpressoSmoothie.sch]
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2013-12-03 Clean up silkscreen, fix a few whoopsies.
    [XpressoSmoothie.kicad_pcb]
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

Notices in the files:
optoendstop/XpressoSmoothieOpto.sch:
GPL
